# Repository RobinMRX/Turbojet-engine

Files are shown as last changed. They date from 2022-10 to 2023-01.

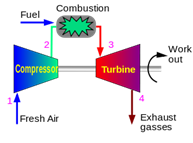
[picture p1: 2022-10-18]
images/theory.png

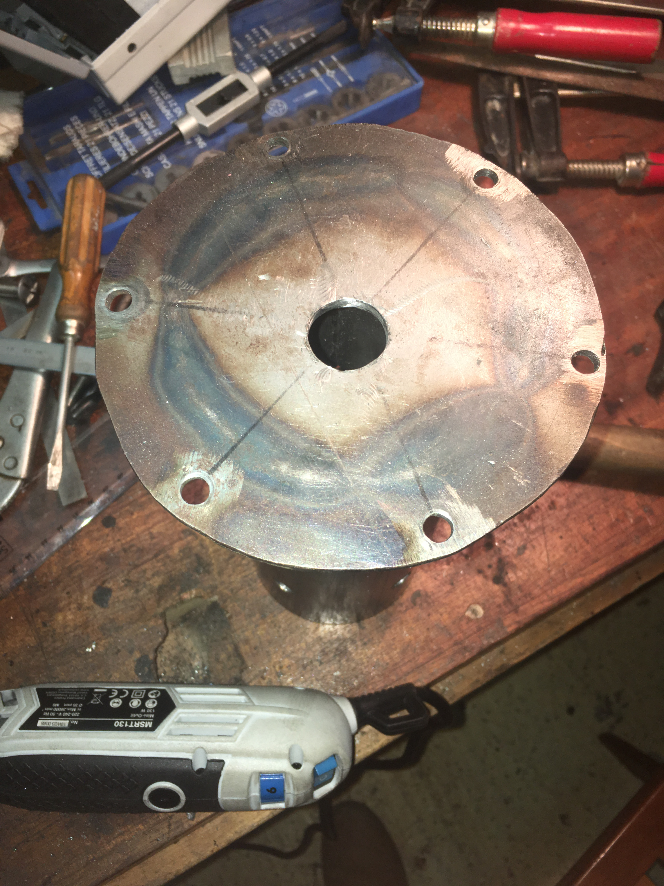
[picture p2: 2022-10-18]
images/IMG_4280.JPG

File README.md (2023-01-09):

# Introduction

Here you will find the design and development of a DIY **```turbojet engine.```**
Feel free to participate and ask me anything about the project.

**Demo video :**

Watch the video (https://youtu.be/5YPhWXnR1MU)

I started this project even before being trained on many of the topics covered. Through this project I was able to develop my skills on a wide range of engineering.
```Mechanical```
```Design```
```Metalworking```
```Fluid mechanics```
```Chemistry```
```Electronics```
```Programming```
```Organization```

## Table of Contents
- [V1](#V1)
  - [A bit of theory](#theory)
  - [How to do it ?](#how)
  - [Start the design](#design)
  - [Industrial design](#drawing)
  - [Manufacturing](#Manufacturing)
  - [How to run it ?](#run)
  - [Test](#Test)
- [V2](#V2)
  - [Spark](#Spark)
  - [Air](#Air)
  - [Gaz](#Gaz)
  - [Communication](#Communication)
  - [Test bench](#bench)

# V1

The first objective of this project is to produce a functional miniature turbojet engine. That is to say, which is **```self-sustaining```**

## A bit of theory 

![Image theory](images/theory.png)

The turbojet transforms the chemical energy of a fuel into kinetic energy. The thrust created by the turbojet comes from the acceleration of a quantity of air between the inlet and the outlet of the system.

To do this, we entered the system with a compressor that allows us to inject a sufficient quantity of air. Then a large amount of energy is released by the combustion of a fuel with the air sent by the compressor. Part of the energy is recovered by a turbine at the system output which will drive the input compressor. The other part of the energy produces the thrust by expansion in the nozzle.

Thanks to the compressor / turbine system, the air flow is self-sustaining. It's our goal. For the moment we are not interested in generating thrust

## How to do it ? 

the idea is to use a **```car turbocharger.```** Indeed this system integrates a compressor and a turbine on the same axis as desired. The problem is that there is no combustion chamber between the compressor and the turbine. To solve this problem we will **```deport the combustion chamber.```**

After recovering a turbocharger from the scrapyard, we can take it apart in order to clean it and keep only what interests us
![Image](images/IMG_3710.JPG)
![Image](images/IMG_3721.JPG)
![Image](images/IMG_3722.JPG)
![Image](images/IMG_3723.JPG)

## Start of the design 

Now that we have prepared our turbocharger, we need to create a combustion chamber between the compressor and the turbine.
We will rely on documentation found on the internet:

![Image](images/Image1.png)
![Image](images/Image2.png)

Note that the combustion chamber is made up of a casing through which passes a **```flame tube.```** This one is pierced, which allows the correct mixing of air and fuel. There are 3 zones in the combustion chamber. from combustion to ejection we have: 
1. **```Primary zone```**
2. **```Secondary zone```**
3. **```Dilution zone```**

Although we understand how it works, we need to know a minimum of the proportions to respect to size the combustion chamber in relation to our turbocharger. To do this, we redo **[this](https://www.youtube.com/watch?v=6GywwbhqR_o&ab_channel=colinfurze)** video of the youtuber Colinfurze.

![Image](images/Diametre.png)

We measure the diameter $D =  2R$ of the inlet of the compressor $$R = 1.75 cm$$

We calculate the air inlet surface of the compressor $$S = \pi R^2 = 9.62 cm^3$$

The surface of the air inlet of the primary zone must be 30% of the surface of the surface of the air inlet of the compressor, therefore:
$$S_{1} = \frac{30}{100}\ S = 2.89 cm^2$$

This surface is divided into 2 rows of 13 holes around the flame tube. So each hole must have an area of:

$$S_{a} = \frac{S_{1}}{26}\ = 0.11 cm^3$$

So a diameter $D_{1} = 0.37 cm = 3.7mm$

We do the same for the secondary zone which must have an air inlet of 20% of that of the compressor inlet.

$$S_{2} = \frac{20}{100}\ S = 1.92 cm^2$$

This surface is divided into 5 holes: $$S_{b} = \frac{S_{2}}{5}\ = 0.38 cm^3$$

So holes with a diameter $D_{2} = 0.70 cm = 7.0 mm$

We do the same for the dilution zone which must have an air inlet of 50% of that of the compressor inlet.

$$S_{3} = \frac{50}{100}\ S = 4.81 cm^2$$

This surface is divided into 5 holes: $$S_{c} = \frac{S_{3}}{5}\ = 0.96 cm^3$$

So holes with a diameter $D_{3} = 1.11 cm = 11.1 mm$

After which the length and diameters of the tubes are dimensioned according to the following rules:

Flame tube length $L = 6D = 210mm$

Flame tube diameter $D_{f} = 2D = 70 mm$

Casing tube diameter $D_{casing} = D_{f} + 30 = 100 mm$

At the metal merchant we choose 3mm thick steel tubes. It may be a little oversized but it will save us some trouble.

The dimensions that come closest to our theoretical dimensions are a tube of 80 mm in diameter for the flame tube and 108 mm for the casing.

## Industrial design 

Now that we have the dimensions, we can move on to the drawing part to have **```plans```** that we will use later.

![Image](images/Tube_à_flamme.png)
![Image](images/Chambre_de_combustion_1.png)
![Image](images/Chambre_de_combustion_2.png)

We take advantage of this to provide a cooling system for the gas circuit.

![Image](images/circuit_de_refroidissement.jpg)

## Manufacturing

here photos of the manufacture and implementation of the combustion chamber on the turbocharger:

![Image](images/IMG_3909.JPG)
![Image](images/IMG_3913.JPG)
![Image](images/IMG_3920.JPG)
![Image](images/IMG_3925.JPG)
![Image](images/IMG_3930.JPG)
![Image](images/IMG_3931.JPG)
![Image](images/IMG_3939.JPG)
![Image](images/IMG_3943.JPG)
![Image](images/IMG_3944.JPG)
![Image](images/IMG_3955.JPG)
![Image](images/IMG_3958.JPG)
![Image](images/IMG_3962.JPG)
![Image](images/IMG_3966.JPG)
![Image](images/IMG_3970.JPG)
![Image](images/IMG_3974.JPG)
![Image](images/IMG_3981.JPG)
![Image](images/IMG_3993.JPG)
![Image](images/IMG_3995.JPG)
![Image](images/IMG_4006.JPG)
![Image](images/IMG_4015.JPG)
![Image](images/IMG_4018.JPG)
![Image](images/IMG_4023.JPG)
![Image](images/IMG_4035.JPG)
![Image](images/IMG_4041.JPG)
![Image](images/IMG_4044.JPG)
![Image](images/IMG_4047.JPG)
![Image](images/IMG_4280.JPG)
![Image](images/IMG_4287.JPG)
![Image](images/IMG_4532.JPG)

## How to run it ? 

To start the turbo, you must start by turning the compressor enough to bring air into the combustion chamber. At the same time we must inject the right amount of fuel (we use butane because the latter being fragrant it allows us to realize if there is a leak) and for the mixture to ignite, we must trigger a spark.

To make the compressor run, a blower from another compressor is used (max pressure 10 bars).

To manage the quantity of gas injected, a quarter-turn valve is used.

To create a spark, we use a car candle, lit by a small device that can be found cheap on amazon and whose energy comes from a conventional battery. The electrodes of the spark plug are well spaced in order to create the largest possible spark.

![Image](images/Image3.png)

These 3 devices are grouped together on a control table near the turbojet

## Test

### Test 1

We make a **```soft start```**, that is to say that we send very little air and very little gas just to start combustion. Combustion starts but the turbine does not recover any power and does not allow the compressor to run to self-maintain the air flow

### Test 2

I sent as much air as possible with the blower on the compressor to give it enough energy to start. I slowly open the throttle valve while activating the spark. When the air / fuel ratio is good, **```the turbojet starts```**, **```it is self-sustaining.```** **```The goal is reached.```**

What is unfortunate is that we do **```not feel any power.```** While my valve is fully open.

**Demo video :**

[![Watch the video](https://img.youtube.com/vi/5YPhWXnR1MU/maxresdefault.jpg)](https://youtu.be/5YPhWXnR1MU)

### Test 3

The purpose of this test is to get more power. To do this, we need to increase the amount of fuel entering the combustion chamber. Since I'm already fully on the throttle valve, I can only play with the diameter of my injector. The problem is that as soon as I increase this size, the regulator on my gas bottle goes into safety.

# V2

The objective of the V2 is to **```increase the power```** of the turbojet engine. We can then add a nozzle to create thrust.

To do this I bought a **```new regulator```**, which allows a much higher flow and pressure than the previous one.

The problem is that now I can't find the right mixtures by hand. I think there is too much fuel compared to the air. Moreover, by considerably increasing the amount of fuel that can be injected, we have **```increased the danger```** of handling. If the pressure suddenly increases, the combustion chamber could explode.

**Demo video :**

[![Watch the video](https://img.youtube.com/vi/BzaCEIvwCl0/maxresdefault.jpg)](https://youtu.be/BzaCEIvwCl0)

The idea of the V2 is therefore to make the turbojet **```remotely controllable```** with the use of the new regulator.

We therefore have 3 things to control:
- **```The spark```**
- **```The air```**
- **```The gas flow```**

## Spark

The spark is triggered by an electrical contact (by pressing a button). You can easily close the electrical contact with a **```relay.```**

## Air

At first I wanted to be able to manage the airflow. So I used a **```servomotor```** to more or less control the opening of the blower. It worked but I had some **```reliability issues.```**

**Demo video :**

[![Watch the video](https://img.youtube.com/vi/y2Q_39y3OnU/maxresdefault.jpg)](https://youtu.be/y2Q_39y3OnU)

Finally we saw during our previous test that to start the turbojet we had to send as much air as possible into the compressor. So we can use a **```solenoid valve```** to on/off control the air supply

## Gaz

The gas part is more complex. Because it is necessary that we can precisely manage the flow of gas.

There are proportional solenoid valves but they are quite expensive. Instead we are going to use our manual quarter-turn valve that we were already using but we are going to couple it to a **```motorization```** to manage its opening. We take this opportunity to add a solenoid valve upstream in order to have the possibility of instantly cutting off the gases.

**How to motorize the valve?**

The idea is to create an **```electric actuator```** that pushes or pulls on the valve to manage its opening.

In a first attempt I used a **```DC motor```** with a screw nut system and a potentiometer installed on the axis of rotation of the valve. This first attempt was functional but **```not reliable and precise enough```**. Indeed, I had trouble aligning the axis of the screw with that of the motor, which induced a lot of vibration. Moreover, I did not succeed in controlling the opening angle of the valve according to the command requested.

**Demo video :**

[![Watch the video](https://img.youtube.com/vi/Buvl3nQfvQg/maxresdefault.jpg)](https://youtu.be/Buvl3nQfvQg)

The current system is visually quite similar but is quite different. The DC motor is replaced by a **```stepper motor```**. This change means that we no longer need to control the position of the valve with the command. Indeed, we can link the opening angle of the valve to the number of steps taken by the motor provided we know the initial opening angle of the valve. Currently I manually put the valve in the closed position at initialization but eventually I will develop an automatic initialization.

In addition, I replaced the classic screw and nut with a screw-nut system with **```several threads```**, as can be found on a 3D printer. It is more suitable because you can pass a lot more torque by turning the screw less quickly.

**Demo video :**

[![Watch the video](https://img.youtube.com/vi/UdKoBPVw2Po/maxresdefault.jpg)](https://youtu.be/UdKoBPVw2Po)
[![Watch the video](https://img.youtube.com/vi/P5eirryI0JA/maxresdefault.jpg)](https://youtu.be/P5eirryI0JA)

## Communication

Now that we know how to control the spark, the air and the gas, we must choose a **```technology```** for remote control.

The first idea was to create a remote control that communicates via **```bluetooth```**. The remote control has been made. based on an arduino nano and an hc-05 bluetooth module.

**codes [here](Bluetooth_communication/)**

![Image](images/IMG_8452.JPEG)
![Image](images/IMG_8251.JPEG)

**Demo video :**

[![Watch the video](https://img.youtube.com/vi/LgDKdboIwjw/maxresdefault.jpg)](https://youtu.be/LgDKdboIwjw)

After some tests, I noticed that there could be **```data loss```** problems in the communication, disconnection problems. In short, this technology was not reliable enough. And we don't want to lose control during the manipulation. So I looked for another technology.

The new and last idea is to use **```WiFi```**. We use an **```ESP32```** in access point mode. We host a web page on it. To control the turbojet, you connect to the ESP32's wifi (in optimal conditions you can reach a range of 100m) and you load the web page on which you can interact with buttons. After a few tests I did not notice any problem on the contrary, **```it works very well```**.

I thank **```Tommy desrochers```** who thanks to these **[tutorials](https://tommydesrochers.com/premiers-tests-pour-bien-debuter-avec-lesp32-ep1/)** allowed me to take control of the ESP32.

code **[here](ESP32_Control_Turbo_V2/)**

**Demo video :**

## Test bench 

Now that we have everything to **```control the turbojet```**, it's time to put everything together on a test bench to start our tests. On this test bench we will find ```the valve control system```, ```the spark control system```, ```the gas control system```, ```a custom PCB``` for our ESP32, ```a purchased relay PCB```, ```a 12V power supply```. We also order ```traffic lights``` that operate at 230V in order to have a ```visual indicator``` when we are away from the turbojet.

**[Here](SolidWorks/) the SolidWorks files**

![Image](images/PCB_schematic.png)
![Image](images/PCB_root.png)

**[Here](Gerber_PCB_TurboV2.zip) the Gerber files for the PCB.** Note that the 3.3v -> 5V shifter output is useless

**Finally we get this:**

![Image](images/IMG_9866.JPEG)
![Image](images/IMG_9867.JPEG)

We add the **spark system**, **End of stroke** detection for gaz opening.

![Image](images/IMG_2318.JPEG)
![Image](images/IMG_2319.JPEG)
![Image](images/IMG_2320.JPEG)
![Image](images/IMG_2321.JPEG)

We also take the opportunity to review the **sprinkler system**. (See photo below) Now the nozzle is a 12mm tube plugged then pierced on one side. The idea is to be able to manufacture several tubes with **different nozzle sizes**. To start, we use a nozzle with 4 holes of 2mm each. This new design allows us to **position** the gas inlet at the air inlet for **better mixing**. In addition, with the flexible tube and the fittings, we can **easily** change the nozzle.

![Image](images/IMG_2308.JPEG)
![Image](images/IMG_2309.JPEG)
![Image](images/IMG_2310.JPEG)
![Image](images/IMG_2313.JPEG)
![Image](images/IMG_2317.JPEG)
![Image](images/IMG_2316.JPEG)

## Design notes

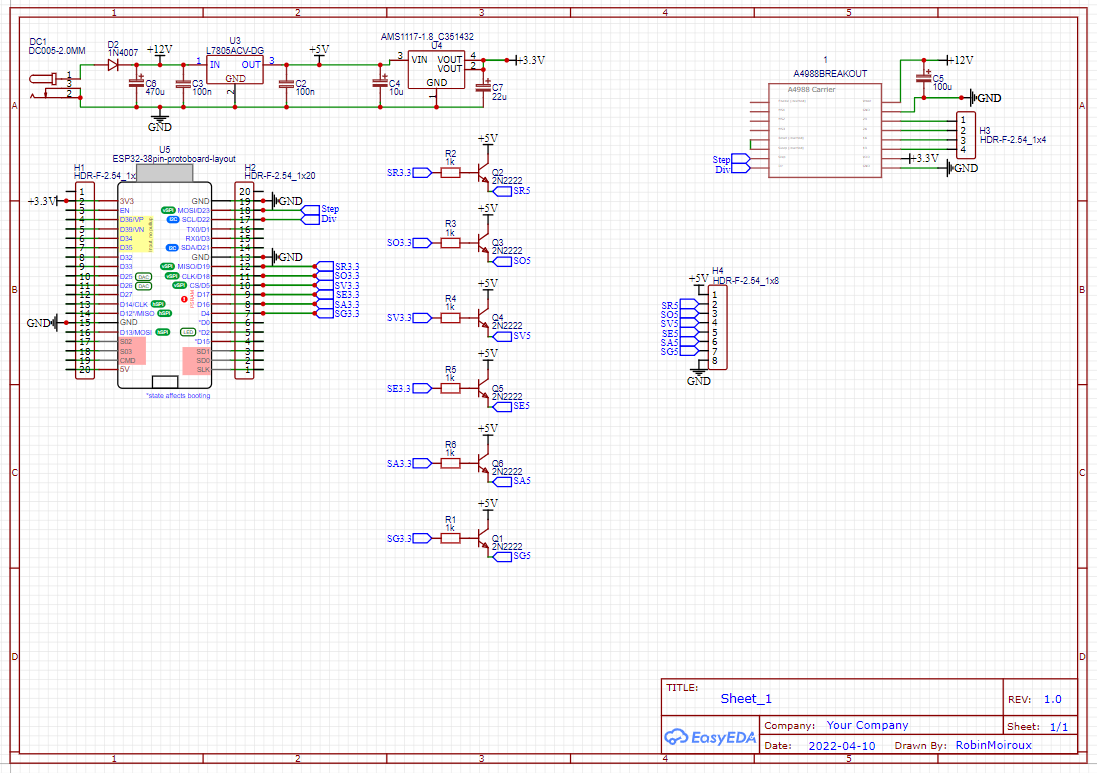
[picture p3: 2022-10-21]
images/PCB_schematic.png

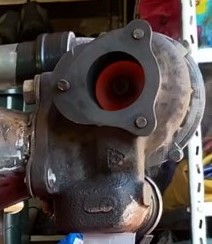
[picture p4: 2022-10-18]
images/OATF9214_Moment.jpg

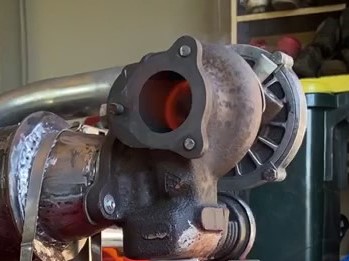
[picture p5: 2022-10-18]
images/RMSZ2370_Moment (2).jpg

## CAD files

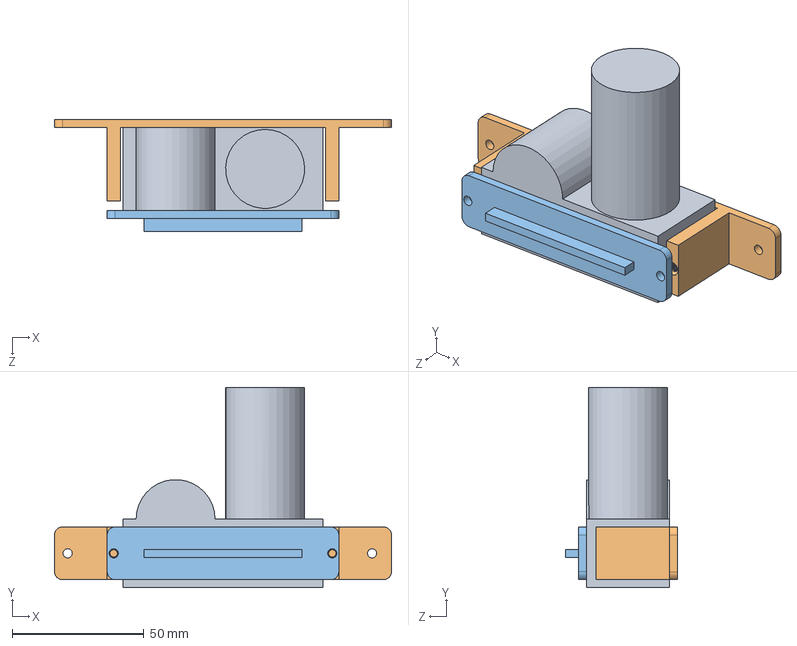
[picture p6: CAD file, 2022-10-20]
SolidWorks/ASM_etincelle.SLDASM
128.0 x 76.0 x 42.5 mm
module_etincelle
fix_module_etincelle
couvercle_module_etincelle

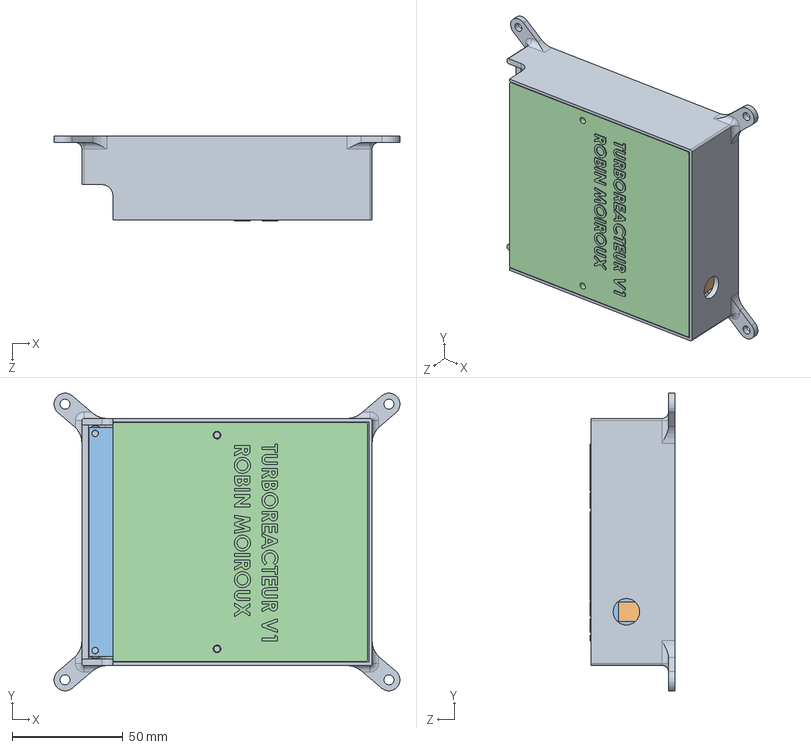
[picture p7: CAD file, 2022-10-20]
SolidWorks/ASM_boitier_electronique.SLDASM
156.2 x 134.4 x 38.5 mm
boitier_electronique
carte_turbo
carte_relais
couvercle

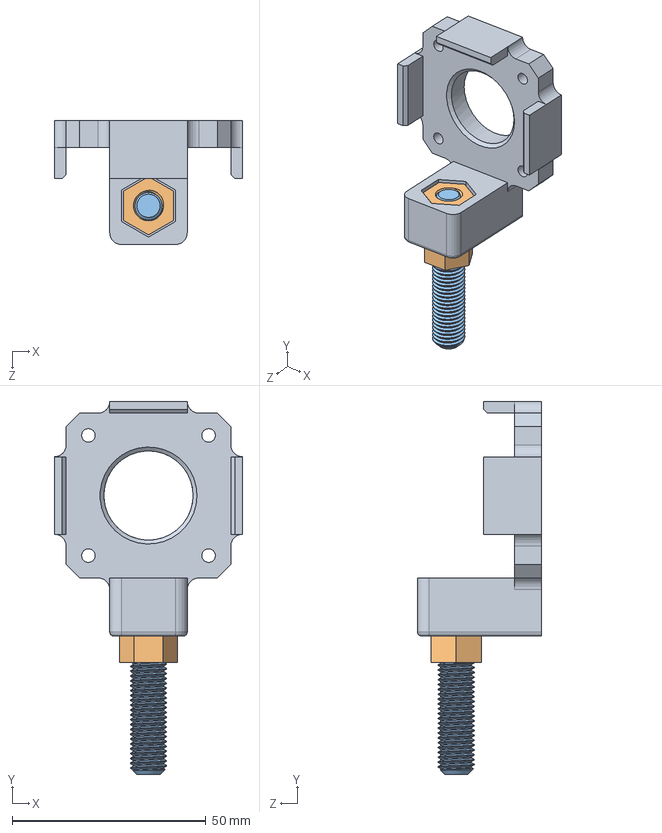
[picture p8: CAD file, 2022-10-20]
SolidWorks/ASM_fix_stepper.SLDASM
48.5 x 96.2 x 32.0 mm
fix_stepper_2
ecrou_M8 x 2
tige_filetee_M8

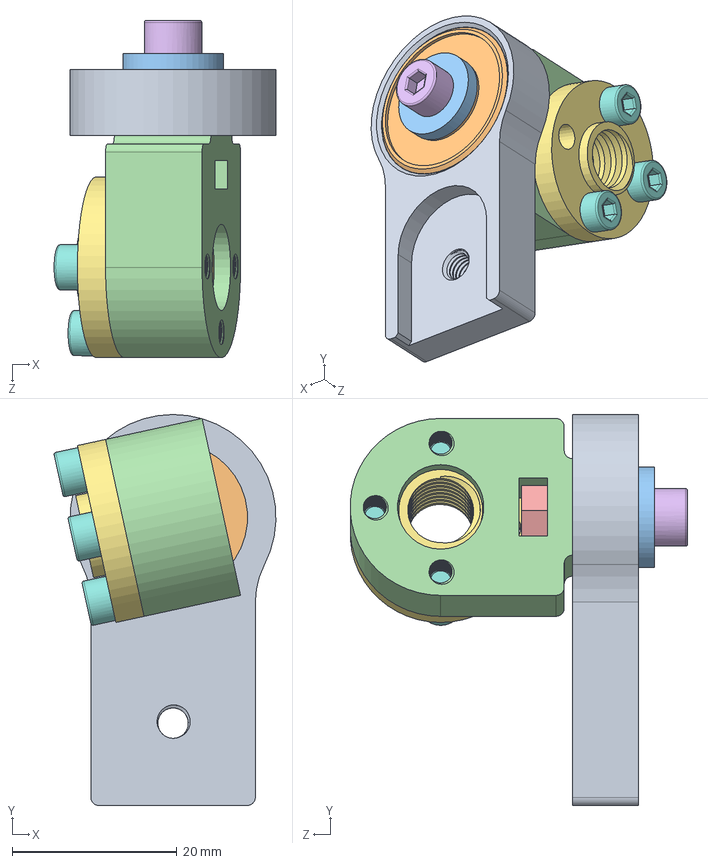
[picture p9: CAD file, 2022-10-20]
SolidWorks/ASM_poignee.SLDASM
26.9 x 47.5 x 41.0 mm
fix_poignee_2
roulement
rondelle_2
fix_ecrou_2
ecrou_M4
M4_16
ecrou_cuivre
M3_10 x 3

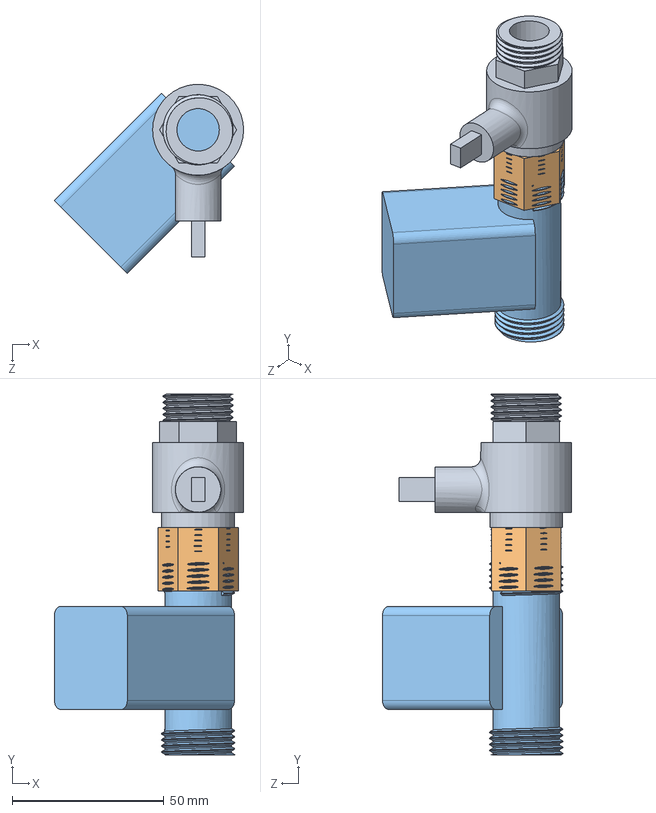
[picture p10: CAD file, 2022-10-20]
SolidWorks/ASM_valve.SLDASM
62.4 x 119.0 x 62.3 mm
valve
raccord_male_male
electro_vanne

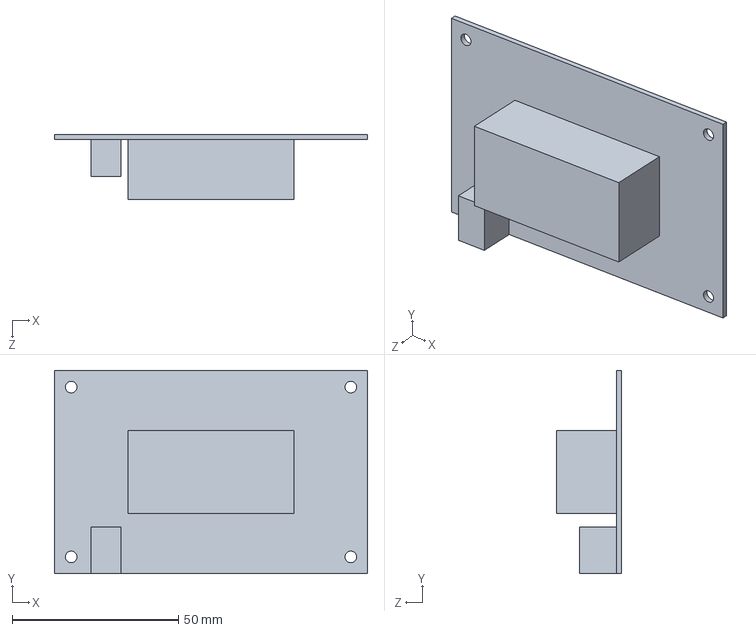
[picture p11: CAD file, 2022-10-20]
SolidWorks/carte_turbo.SLDPRT
94.0 x 61.0 x 19.6 mm

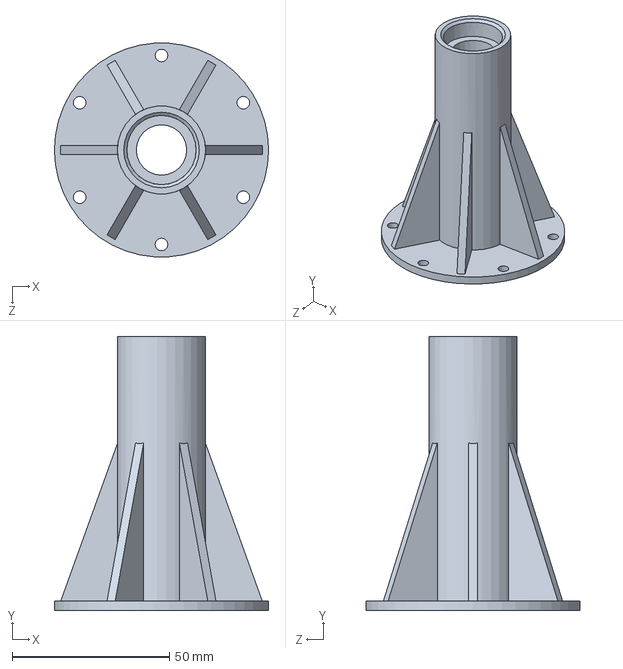
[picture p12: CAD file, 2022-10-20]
SolidWorks/support_stepper.SLDPRT
68.0 x 87.0 x 67.8 mm

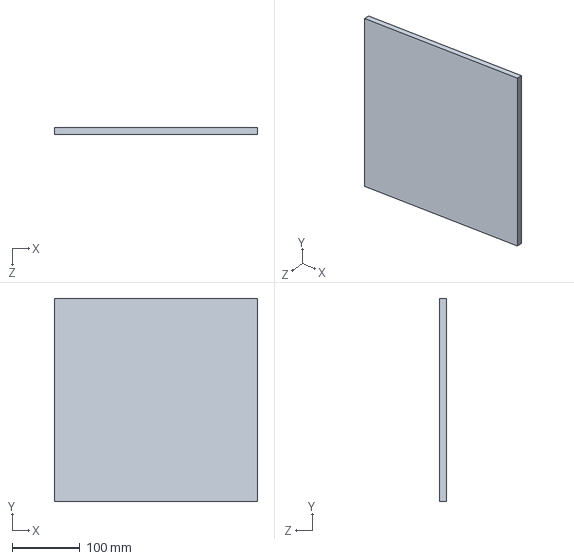
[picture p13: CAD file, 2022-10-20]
SolidWorks/socle.SLDPRT
300.0 x 300.0 x 10.0 mm

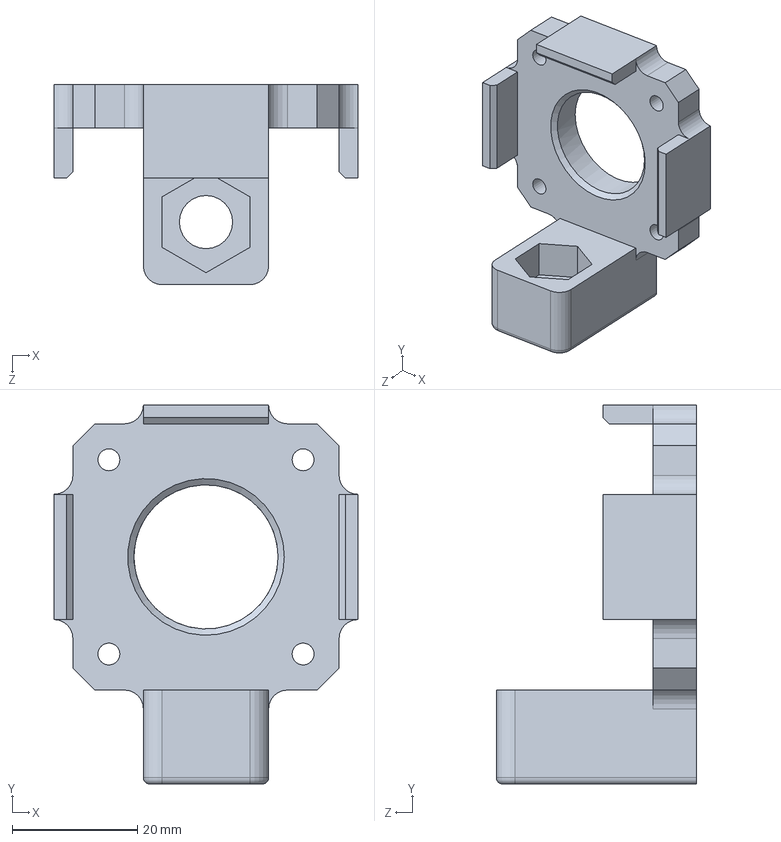
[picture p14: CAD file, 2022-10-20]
SolidWorks/fix_stepper_2.SLDPRT
48.5 x 60.5 x 32.0 mm

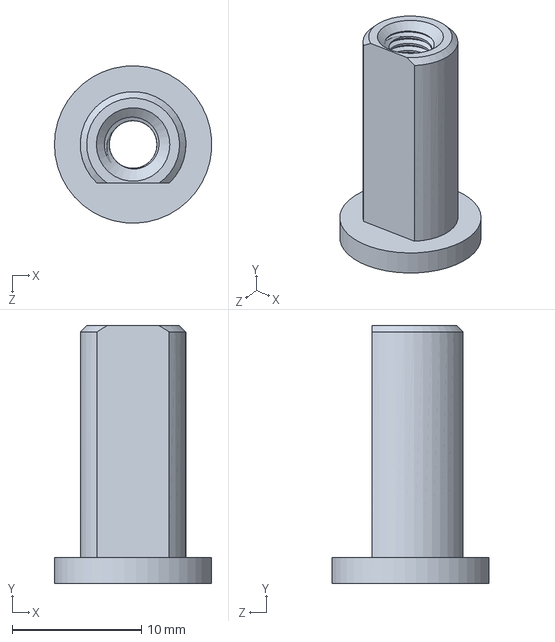
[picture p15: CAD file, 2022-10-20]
SolidWorks/axe_rlmnt_2.SLDPRT
12.2 x 20.0 x 12.2 mm

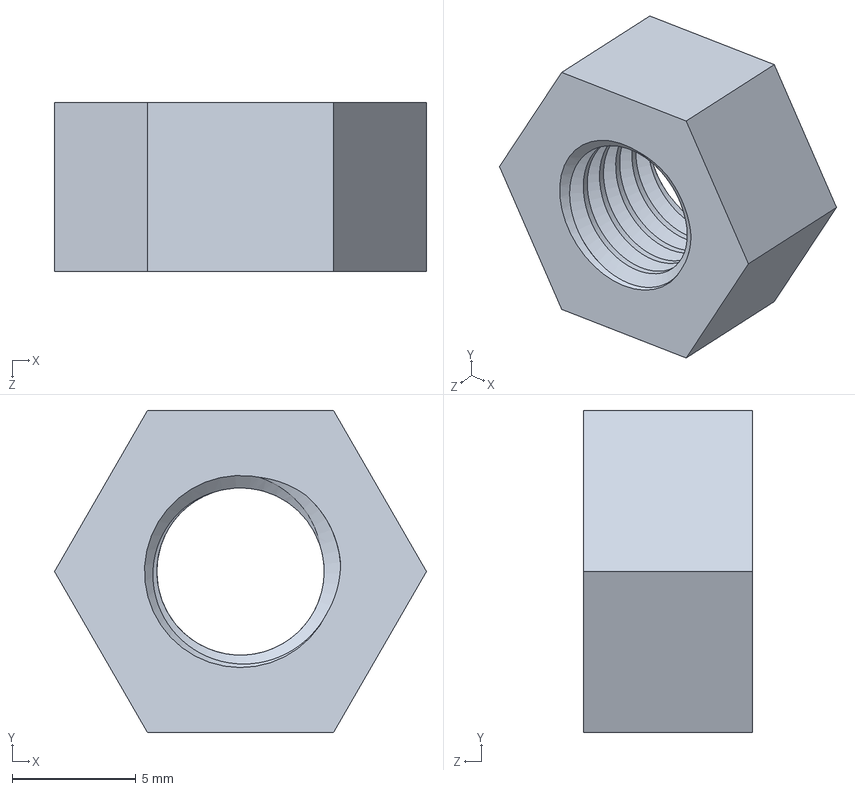
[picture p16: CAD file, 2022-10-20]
SolidWorks/ecrou_M8.SLDPRT
15.0 x 13.0 x 6.80 mm

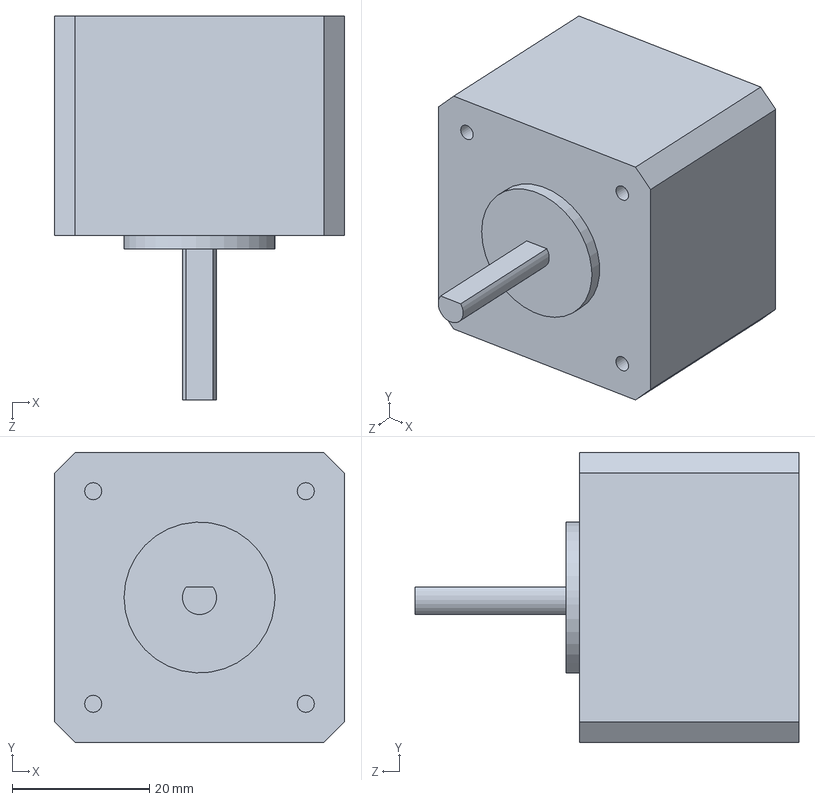
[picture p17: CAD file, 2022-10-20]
SolidWorks/stepper_42.SLDPRT
42.3 x 42.3 x 56.0 mm

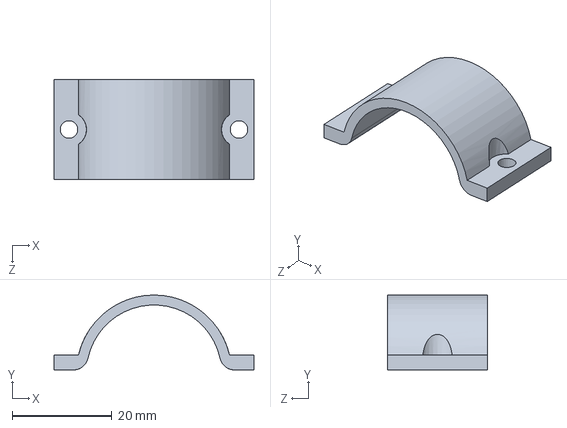
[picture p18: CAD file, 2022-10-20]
SolidWorks/fix_valve_2.SLDPRT
40.0 x 15.0 x 20.0 mm

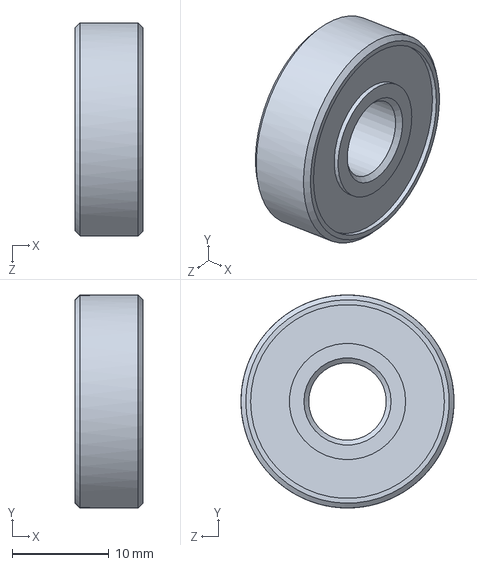
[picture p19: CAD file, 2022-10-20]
SolidWorks/roulement.SLDPRT
7.00 x 22.0 x 22.0 mm

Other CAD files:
SolidWorks/fix_stepper.SLDPRT
SolidWorks/carte_relais.SLDPRT
SolidWorks/valve.SLDPRT
SolidWorks/raccord_male_male.SLDPRT
SolidWorks/Alim.SLDPRT
SolidWorks/Axe.SLDPRT
SolidWorks/M3_10.SLDPRT
SolidWorks/M4_10.SLDPRT
SolidWorks/M4_16.SLDPRT
SolidWorks/axe_rlmnt.SLDPRT
SolidWorks/boitier_electronique.SLDPRT
SolidWorks/connecteur_souple.SLDPRT
SolidWorks/couvercle.SLDPRT
SolidWorks/couvercle_module_etincelle.SLDPRT
SolidWorks/ecrou_M4.SLDPRT
SolidWorks/ecrou_cuivre.SLDPRT
SolidWorks/electro_vanne.SLDPRT
SolidWorks/fix_ecrou.SLDPRT
SolidWorks/fix_ecrou_2.SLDPRT
SolidWorks/fix_fin_de_course.SLDPRT
SolidWorks/fix_module_etincelle.SLDPRT
SolidWorks/fix_poignee.SLDPRT
SolidWorks/fix_poignee_2.SLDPRT
SolidWorks/fix_valve_1.SLDPRT
SolidWorks/fix_valve_3.SLDPRT
SolidWorks/module_etincelle.SLDPRT
SolidWorks/poignee_gaz.SLDPRT
SolidWorks/raccord_gaz.SLDPRT
SolidWorks/raccord_gaz_bouteille.SLDPRT
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

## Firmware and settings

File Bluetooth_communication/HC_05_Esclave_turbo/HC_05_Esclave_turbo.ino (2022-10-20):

#include <SoftwareSerial.h>
#include <Servo.h>  // on inclut la bibliothèque pour piloter un servomoteur

SoftwareSerial ArduinoMaitre(10, 11);
Servo servoAir;

String msg;

const int Etincelle = 2;

const int Pot = A0;
int val_pot;
int val_pot_deg;

int motor_O = 8; // Sens de l'ouverture de la vanne. (IN?)
int motor_F = 9; // Sens de la fermeture de la vanne. (IN?)
int enablePin = 5;

const int BP_pos_0 = 4;
int etat_BP_pos_0;

int data_etincelle;
int data_air;
int data_gaz;

void setup() {

  ArduinoMaitre.begin(9600);

  servoAir.attach(3);
  servoAir.write(0);

  pinMode (Etincelle, OUTPUT);
  digitalWrite (Etincelle, LOW);

  pinMode (Pot, INPUT);

  pinMode(motor_O, OUTPUT);
  pinMode(motor_F, OUTPUT);
  pinMode(enablePin, OUTPUT);

  pinMode (BP_pos_0, INPUT_PULLUP);

}

void verin_action (int capteur, int commande) {

  while (capteur < commande) {
    digitalWrite(motor_O, HIGH);
    digitalWrite(motor_F, LOW);

    val_pot_deg = analogRead(A0);
    capteur = map(val_pot_deg, 0, 1023, 0, 415);

  }

  while (capteur > commande) {
    digitalWrite(motor_O, LOW);
    digitalWrite(motor_F, HIGH);

    val_pot_deg = analogRead(A0);
    capteur = map(val_pot_deg, 0, 1023, 0, 415);
  }
}

void loop() {

  // LECTURE DES DATA
  LectureMaitre();

  val_pot = analogRead(Pot);
  val_pot_deg = map(val_pot, 0, 1023, 0, 415);

  analogWrite (enablePin, 255);
  digitalWrite(motor_O, HIGH);
  digitalWrite(motor_F, HIGH);

  // ACTION
  if (msg != "") {

    char Data[msg.length() + 1];
    msg.toCharArray(Data, msg.length() + 1);

    sscanf(Data, "%03d:%03d:%03d", &data_etincelle, &data_air, &data_gaz);

  }

  // ETINCELLE
  if (data_etincelle == 101) {
    digitalWrite(Etincelle, HIGH);
  }
  else if (data_etincelle == 102) {
    digitalWrite(Etincelle, LOW);
  }

  // AIR
  if (data_air == 203) {
    servoAir.write(180);
  }
  else if (data_air == 204) {
    servoAir.write(0);
  }

  // GAZ
  if (data_gaz == 300) {
    etat_BP_pos_0 = digitalRead(BP_pos_0);
    while (etat_BP_pos_0 == HIGH ) {
      digitalWrite(motor_O, LOW);
      digitalWrite(motor_F, HIGH);

      etat_BP_pos_0 = digitalRead(BP_pos_0);
    }
  }
  if (data_gaz == 301) {
    verin_action (val_pot_deg, 1);
  } else if (data_gaz == 302) {
    verin_action (val_pot_deg, 2);
  } else if (data_gaz == 303) {
    verin_action (val_pot_deg, 3);
  } else if (data_gaz == 304) {
    verin_action (val_pot_deg, 4);
  } else if (data_gaz == 305) {
    verin_action (val_pot_deg, 5);
  } else if (data_gaz == 306) {
    verin_action (val_pot_deg, 6);
  } else if (data_gaz == 307) {
    verin_action (val_pot_deg, 7);
  } else if (data_gaz == 308) {
    verin_action (val_pot_deg, 8);
  } else if (data_gaz == 309) {
    verin_action (val_pot_deg, 9);
  } else if (data_gaz == 310) {
    verin_action (val_pot_deg, 10);
  } else if (data_gaz == 311) {
    verin_action (val_pot_deg, 11);
  } else if (data_gaz == 312) {
    verin_action (val_pot_deg, 12);
  } else if (data_gaz == 313) {
    verin_action (val_pot_deg, 13);
  } else if (data_gaz == 314) {
    verin_action (val_pot_deg, 14);
  } else if (data_gaz == 315) {
    verin_action (val_pot_deg, 15);
  } else if (data_gaz == 316) {
    verin_action (val_pot_deg, 16);
  } else if (data_gaz == 317) {
    verin_action (val_pot_deg, 17);
  } else if (data_gaz == 318) {
    verin_action (val_pot_deg, 18);
  } else if (data_gaz == 319) {
    verin_action (val_pot_deg, 19);
  } else if (data_gaz == 320) {
    verin_action (val_pot_deg, 20);
  } else if (data_gaz == 321) {
    verin_action (val_pot_deg, 21);
  } else if (data_gaz == 322) {
    verin_action (val_pot_deg, 22);
  } else if (data_gaz == 323) {
    verin_action (val_pot_deg, 23);
  } else if (data_gaz == 324) {
    verin_action (val_pot_deg, 24);
  } else if (data_gaz == 325) {
    verin_action (val_pot_deg, 25);
  } else if (data_gaz == 326) {
    verin_action (val_pot_deg, 26);
  } else if (data_gaz == 327) {
    verin_action (val_pot_deg, 27);
  } else if (data_gaz == 328) {
    verin_action (val_pot_deg, 28);
  } else if (data_gaz == 329) {
    verin_action (val_pot_deg, 29);
  } else if (data_gaz == 330) {
    verin_action (val_pot_deg, 30);
  } else if (data_gaz == 331) {
    verin_action (val_pot_deg, 31);
  } else if (data_gaz == 332) {
    verin_action (val_pot_deg, 32);
  } else if (data_gaz == 333) {
    verin_action (val_pot_deg, 33);
  } else if (data_gaz == 334) {
    verin_action (val_pot_deg, 34);
  } else if (data_gaz == 335) {
    verin_action (val_pot_deg, 35);
  } else if (data_gaz == 336) {
    verin_action (val_pot_deg, 36);
  } else if (data_gaz == 337) {
    verin_action (val_pot_deg, 37);
  } else if (data_gaz == 338) {
    verin_action (val_pot_deg, 38);
  } else if (data_gaz == 339) {
    verin_action (val_pot_deg, 39);
  } else if (data_gaz == 340) {
    verin_action (val_pot_deg, 40);
  } else if (data_gaz == 341) {
    verin_action (val_pot_deg, 41);
  } else if (data_gaz == 342) {
    verin_action (val_pot_deg, 42);
  } else if (data_gaz == 343) {
    verin_action (val_pot_deg, 43);
  } else if (data_gaz == 344) {
    verin_action (val_pot_deg, 44);
  } else if (data_gaz == 345) {
    verin_action (val_pot_deg, 45);
  } else if (data_gaz == 346) {
    verin_action (val_pot_deg, 46);
  } else if (data_gaz == 347) {
    verin_action (val_pot_deg, 47);
  } else if (data_gaz == 348) {
    verin_action (val_pot_deg, 48);
  } else if (data_gaz == 349) {
    verin_action (val_pot_deg, 49);
  } else if (data_gaz == 350) {
    verin_action (val_pot_deg, 50);
  } else if (data_gaz == 351) {
    verin_action (val_pot_deg, 51);
  } else if (data_gaz == 352) {
    verin_action (val_pot_deg, 52);
  } else if (data_gaz == 353) {
    verin_action (val_pot_deg, 53);
  } else if (data_gaz == 354) {
    verin_action (val_pot_deg, 54);
  } else if (data_gaz == 355) {
    verin_action (val_pot_deg, 55);
  } else if (data_gaz == 356) {
    verin_action (val_pot_deg, 56);
  } else if (data_gaz == 357) {
    verin_action (val_pot_deg, 57);
  } else if (data_gaz == 358) {
    verin_action (val_pot_deg, 58);
  } else if (data_gaz == 359) {
    verin_action (val_pot_deg, 59);
  } else if (data_gaz == 360) {
    verin_action (val_pot_deg, 60);
  } else if (data_gaz == 361) {
    verin_action (val_pot_deg, 61);
  } else if (data_gaz == 362) {
    verin_action (val_pot_deg, 62);
  } else if (data_gaz == 363) {
    verin_action (val_pot_deg, 63);
  } else if (data_gaz == 364) {
    verin_action (val_pot_deg, 64);
  } else if (data_gaz == 365) {
    verin_action (val_pot_deg, 65);
  } else if (data_gaz == 366) {
    verin_action (val_pot_deg, 66);
  } else if (data_gaz == 367) {
    verin_action (val_pot_deg, 67);
  } else if (data_gaz == 368) {
    verin_action (val_pot_deg, 68);
  } else if (data_gaz == 369) {
    verin_action (val_pot_deg, 69);
  } else if (data_gaz == 370) {
    verin_action (val_pot_deg, 70);
  } else if (data_gaz == 371) {
    verin_action (val_pot_deg, 71);
  } else if (data_gaz == 372) {
    verin_action (val_pot_deg, 72);
  } else if (data_gaz == 373) {
    verin_action (val_pot_deg, 73);
  } else if (data_gaz == 374) {
    verin_action (val_pot_deg, 74);
  } else if (data_gaz == 375) {
    verin_action (val_pot_deg, 75);
  } else if (data_gaz == 376) {
    verin_action (val_pot_deg, 76);
  } else if (data_gaz == 377) {
    verin_action (val_pot_deg, 77);
  } else if (data_gaz == 378) {
    verin_action (val_pot_deg, 78);
  } else if (data_gaz == 379) {
    verin_action (val_pot_deg, 79);
  } else if (data_gaz == 380) {
    verin_action (val_pot_deg, 80);
  } else if (data_gaz == 381) {
    verin_action (val_pot_deg, 81);
  } else if (data_gaz == 382) {
    verin_action (val_pot_deg, 82);
  } else if (data_gaz == 383) {
    verin_action (val_pot_deg, 83);
  } else if (data_gaz == 384) {
    verin_action (val_pot_deg, 84);
  } else if (data_gaz == 385) {
    verin_action (val_pot_deg, 85);
  } else if (data_gaz == 386) {
    verin_action (val_pot_deg, 86);
  } else if (data_gaz == 387) {
    verin_action (val_pot_deg, 87);
  } else if (data_gaz == 388) {
    verin_action (val_pot_deg, 88);
  } else if (data_gaz == 389) {
    verin_action (val_pot_deg, 89);
  } else if (data_gaz == 390) {
    verin_action (val_pot_deg, 90);
  }

  msg = "";
  data_etincelle = 0;
  data_air = 0;
  data_gaz = 0;
}


void LectureMaitre() {
  while (ArduinoMaitre.available()) {
    delay(10);
    if (ArduinoMaitre.available() > 0) {
      char c = ArduinoMaitre.read();  //gets one byte from serial buffer
      msg += c; //makes the string readString
    }
  }
  ArduinoMaitre.flush();
}

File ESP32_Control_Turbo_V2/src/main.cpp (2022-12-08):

#include <Arduino.h>
#include <ESPAsyncWebServer.h>
#include <SPIFFS.h>

const char* ssid = "Control_turbo";
const char* password = "Mangemort";

const int air = 4;
const int etincelle = 17;
const int gaz = 16;

const int feuRouge = 18;
const int feuOrange = 19;
const int feuVert = 5;

const int finDeCourse = 2;
int etat_FDC;

int consignePourc = 0;
float consigneTour = 0;
float tour = 0.0;

const int stepPin = 23;
const int dirPin = 22;

int delais = 1500;

AsyncWebServer serveur(80);

float pourcentage2tr(int pourcentage){
  const float maxDeg = 90.0;
  const float pas = 8.0;
  const float r = 85.0;
  const float pi = 3.1415;

  float tour = (maxDeg/100.0)*((2.0*pi*r)/(pas*360.0))*pourcentage;
  return (tour);
}

void start(){
    for (int i=0; i<=2; i++){

        digitalWrite(feuVert, LOW);
        digitalWrite(feuOrange, LOW);
        digitalWrite(feuRouge, LOW);

        delay(1000);

        digitalWrite(feuVert, HIGH);
        digitalWrite(feuOrange, HIGH);
        digitalWrite(feuRouge, HIGH);

        delay(1000);
    }    
}

void zeroStepper(){
    digitalWrite(dirPin, HIGH);
    etat_FDC = digitalRead(finDeCourse);

    while (etat_FDC){
        digitalWrite(stepPin, HIGH);
        delayMicroseconds(delais/2);
        digitalWrite(stepPin, LOW);
        delayMicroseconds(delais/2);

        etat_FDC = digitalRead(finDeCourse);
    }

    consignePourc = 0;
    consigneTour = 0;
    tour = 0.0;
    
}

void setup() {
    //----------------------------------------------------------Serial
    Serial.begin(115200);
    Serial.println('\n');

    //----------------------------------------------------------GPIO
    pinMode(air, OUTPUT);
    digitalWrite(air, HIGH);
    
    pinMode(etincelle, OUTPUT);
    digitalWrite(etincelle, HIGH);

    pinMode(gaz, OUTPUT);
    digitalWrite(gaz, HIGH);

    pinMode(stepPin, OUTPUT);
    pinMode(dirPin, OUTPUT);

    digitalWrite(dirPin, HIGH);

    pinMode(feuRouge, OUTPUT);
    digitalWrite(feuRouge, HIGH);

    pinMode(feuOrange, OUTPUT);
    digitalWrite(feuOrange, HIGH);

    pinMode(feuVert, OUTPUT);
    digitalWrite(feuVert, HIGH);

    pinMode(finDeCourse, INPUT_PULLUP);

    //----------------------------------------------------------SPIFFS
    if(!SPIFFS.begin()){
        Serial.println("Erreur SPIFFS...");
        return;
    }

    File root = SPIFFS.open("/");
    File file = root.openNextFile();

    while (file){
        Serial.print("File: ");
        Serial.println(file.name());
        file.close();
        file = root.openNextFile();
    }
    
    //----------------------------------------------------------Wi-Fi
    Serial.println("Creation du point d'acces...");
    WiFi.softAP(ssid, password); // Création du point d'accès. On peu créer un réseau ouvert si on ne précise pas de mdp. Un nom est généré automatiquement si on ne précise pas de nom.

    Serial.print("Adresse IP: ");
    Serial.println(WiFi.softAPIP()); // Donne l'adresse IP généré par notre point d'accès.

    //----------------------------------------------------------SERVEUR
    serveur.on("/", HTTP_GET, [](AsyncWebServerRequest *request){
        request->send(SPIFFS, "/index.html", "text/html");
    });

    serveur.on("/style.css", HTTP_GET, [](AsyncWebServerRequest *request){
        request->send(SPIFFS, "/style.css", "text/css");
    });

    serveur.on("/script.js", HTTP_GET, [](AsyncWebServerRequest *request){
        request->send(SPIFFS, "/script.js", "text/javascript");
    });

    serveur.on("/robi.ico", HTTP_GET, [](AsyncWebServerRequest *request){
        request->send(SPIFFS, "/robi.ico", "image/ico");
    });

    serveur.on("/onAllu", HTTP_GET, [](AsyncWebServerRequest *request){
        digitalWrite(etincelle, LOW);
        digitalWrite(feuOrange, LOW);
        Serial.println("onAllu");
        request->send(204);
    });

    serveur.on("/offAllu", HTTP_GET, [](AsyncWebServerRequest *request){
        digitalWrite(etincelle, HIGH);
        digitalWrite(feuOrange, HIGH);
        Serial.println("offAllu");
        request->send(204);
    });

    serveur.on("/onAir", HTTP_GET, [](AsyncWebServerRequest *request){
        digitalWrite(air, LOW);
        digitalWrite(feuVert, LOW);
        Serial.println("onAir");
        request->send(204);
    });

    serveur.on("/offAir", HTTP_GET, [](AsyncWebServerRequest *request){
        digitalWrite(air, HIGH);
        digitalWrite(feuVert, HIGH);
        Serial.println("offAir");
        request->send(204);
    });

    serveur.on("/onGaz", HTTP_GET, [](AsyncWebServerRequest *request){
        digitalWrite(gaz, LOW);
        digitalWrite(feuRouge, LOW);
        Serial.println("onGaz");
        request->send(204);
    });

    serveur.on("/offGaz", HTTP_GET, [](AsyncWebServerRequest *request){
        digitalWrite(gaz, HIGH);
        digitalWrite(feuRouge, HIGH);
        zeroStepper();
        Serial.println("offGaz");
        request->send(204);
    });

    serveur.on("/slider", HTTP_GET, [](AsyncWebServerRequest *request){
        String message;
        if(request->hasParam("value")){
            Serial.println("l'ESP a trouvé le paramètre");
            message = request->getParam("value")->value();
            Serial.println("MESSAGE :" + message);
            Serial.println("TOUR :" + String(tour));

            consignePourc = message.toInt();
            Serial.println("CONSIGNE POURCENTAGE : " + String(consignePourc));

            consigneTour = pourcentage2tr(consignePourc);
            Serial.println("CONSIGNE TOUR : " + String(consigneTour));

            float diffTour = consigneTour - tour;
            Serial.println("DIFF TOUR : " + String(diffTour));

            tour += diffTour;
            Serial.println("TOUR :" + String(tour));

            if (diffTour>0){
                digitalWrite(dirPin, LOW);
                for(int i=0; i<round(200*diffTour); i++){
                digitalWrite(stepPin, HIGH);
                delayMicroseconds(delais/2);
                digitalWrite(stepPin, LOW);
                delayMicroseconds(delais/2);
                }
            }else if (diffTour<0){
                digitalWrite(dirPin, HIGH);
                for(int i=0; i<abs(round(200*diffTour)); i++){
                digitalWrite(stepPin, HIGH);
                delayMicroseconds(delais/2);
                digitalWrite(stepPin, LOW);
                delayMicroseconds(delais/2);
                }
                digitalWrite(dirPin, LOW);
            } else {}
        }

        request->send(204);
    });

    /*serveur.on("/lirePotar", HTTP_GET, [](AsyncWebServerRequest *request){
        int val = analogRead(potar);
        String valPotar = String(val);
        request->send(200, "text/plain", valPotar);
    });

    serveur.on("/on", HTTP_GET, [](AsyncWebServerRequest *request){
        digitalWrite(air, HIGH);
        request->send(200);
    });
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
